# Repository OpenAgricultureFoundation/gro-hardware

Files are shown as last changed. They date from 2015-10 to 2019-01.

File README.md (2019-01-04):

# DEPRECATED.

## Personal Food Computer 1.0

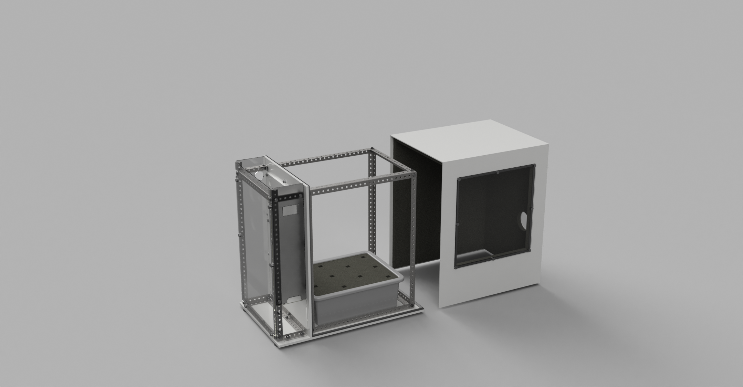
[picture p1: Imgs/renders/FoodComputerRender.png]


## Resources in this repository

- Guides
	- [Shell Assembly Guide](./Guides/ShellAssemblyGuide.md)
	- [Main Frame Assembly Guide](./Guides/MainFrameAssemblyGuide.md)
	- [Motherboard Assembly Guide(PDF only)](./Guides/PDF/MotherboardAssemblyGuide.pdf)
- CAD Models
	- [CAD Models(Solidworks)](./CAD)
	- [Laser Cutter DXF files](./CAD/LASERCUT)
	- [CNC Machine DXF Files](./CAD/CNCs)
- [Bill of Materials](./BOM.xlsx) (There are multiple sheets in the book, check bottom tabs.)

## External Links
- [Overview/Wiki](http://wiki.openag.media.mit.edu/food_computer_1)
- [Build Video](https://youtu.be/Jx-y0jQJlfs)
- ["Build" Page on OpenAg Website](http://openag.media.mit.edu/build/)
- [Adrian Lu protoshield wiring](http://adrianllu.com/2016/04/17/motherboard-build-notes-part-1-micro-controller-protoshield/)
- [JoshSinykin's wiring diagram](http://forum.openag.media.mit.edu/t/about-the-instructions-category/19/2)

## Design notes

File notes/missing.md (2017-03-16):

# Missing parts

## Not on BOM
- 6channel, maletofemale jumper wire
- screws?
  - [long    = 1.5"](http://www.homedepot.com/p/Everbilt-6-x-1-2-in-Zinc-Plated-Phillips-Pan-Head-Drive-Sheet-Metal-Screw-100-Piece-801552/204275068)
  - [medium  = 1.0"](http://www.homedepot.com/p/Everbilt-6-x-1-in-Zinc-Plated-Pan-Head-Phillips-Drive-Sheet-Metal-Screw-100-Piece-801572/204275050)
- reed relay
- GROVE connectors
  - [1 5pk female jumper to grove](https://www.seeedstudio.com/Grove-4-pin-Female-Jumper-to-Grove-4-pin-Conversion-Cable-%285-PCs-per-PAck%29-p-1020.html)
  - [1 5pk male jumper to grove cable](https://www.seeedstudio.com/Grove-4-pin-Male-Jumper-to-Grove-4-pin-Conversion-Cable-(5-PCs-per-Pack)-p-1565.html)
  - [1 5pk 4 pin, buckled, 50cm grove cable](https://www.seeedstudio.com/Grove-Universal-4-Pin-Buckled-50cm-Cable-(5-PCs-Pack)-p-928.html)
  - [1 10pk Grove connector sockets](https://www.seeedstudio.com/Grove-Universal-4-pin-connector-p-789.html)
  - [1 Grove - Temperature&Humidity Sensor Pro](https://www.seeedstudio.com/Grove-Temperature%26Humidity-Sensor-Pro-p-838.html)

# Tools

- Hole Saws

| Size | Usage |
| :--- | :--- |
| - 0.5 in  | Wire management |
| - 0.75 in | Camera |
| - 1.5 in  | Wire management|
| - 1.75 in | Heater |
| - 4.5 in  | Heater |

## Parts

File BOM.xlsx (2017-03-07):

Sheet: Motherboard
Item Name | Distributor | Distributor's Item Name | Units | Cost per Unit ($) | Item Cost
POWER
Power Strip (http://www.amazon.com/CyberPower-CSB606-Protector-6-Outlets-Joules/dp/B00FLTTGYG) | AmazonPrime | CyberPower CSB606 Surge Protector 6-Outlets 6-Ft Cord 900 Joules | 1 | 10.15 | 10.15
Main Power Supply (http://www.amazon.com/Switching-Power-Supply-Strip-Light/dp/B007MWNF5Q) | AmazonPrime | 12V 30A 360W Switching Power Supply for LED Strip Light | 1 | 24.96 | 24.96
AC Extension Cable (http://www.amazon.com/gp/product/B0002J1KS0/ref=ox_sc_act_title_1?ie=UTF8&psc=1&smid=ATVPDKIKX0DER) | AmazonPrime | C2G / Cables To Go 03137 18 AWG Outlet Saver Power Extension Cord for NEMA 5-15P to NEMA 5-15R, Black (1 Foot/0.30 Meters) | 1 | 4.99 | 4.99
BRAINS
Raspberry Pi Power Supply (http://www.amazon.com/CanaKit-Raspberry-Power-Supply-Listed/dp/B00MARDJZ4) | AmazonPrime | CanaKit 5V 2.5A Raspberry Pi 2 Power Supply (UL Listed) | 1 | 9.99 | 9.99
Arduino Mega 2560 (http://www.amazon.com/Ximico-Arduino-Cable-Atmega2560-16au-Compatible/dp/B00KG3SBE8?s=pc) | AmazonPrime | Ximico Mega 2560 R3 for Arduino + USB Cable / Mega 2560 R3 Atmega2560-16au Board (Compatible with Arduino) | 1 | 14.19 | 14.19
Raspberry Pi 2 Model B (http://www.amazon.com/Raspberry-Pi-Model-Desktop-Linux/dp/B00T2U7R7I) | AmazonPrime | Raspberry Pi 2 Model B Desktop (Quad Core CPU 900 MHz, 1 GB RAM, Linux) | 1 | 41.87 | 41.87
Micro SD Card (http://www.amazon.com/Kingston-microSDHC-Memory-SDC4-8GBET/dp/B00200K1TS?s=pc) | AmazonPrime | Kingston 8 GB microSDHC Class 4 Flash Memory Card SDC4/8GBET | 1 | 3.99 | 3.99
Ethernet cable (http://www.amazon.com/gp/product/B00EUHRLF6) | AmazonPrime |  | 1 | 5.99 | 5.99
Arduino Mega Protoshield (http://www.amazon.com/Gikfun-Protoshield-Prototype-Shield-Arduino/dp/B00Q9YBQ04?s=pc) | AmazonPrime | Gikfun Protoshield Prototype Shield DIY KIT A1 for Arduino Mega 1280 2560 R1 - R3 | 1 | 8.99 | 8.99
Grove Base Shield (https://www.seeedstudio.com/item_detail.html?p_id=1378) | SeeedStudio | Base Shield V2 | 1 | 8.9 | 8.9
Touchscreen Display (https://www.adafruit.com/products/2097) | Adafruit | PiTFT - Assembled 480x320 3.5" TFT+Touchscreen for Raspberry Pi | 1 | 44.95 | 44.95
GPIO Cable (http://www.amazon.com/ribbon-cable-Raspberry-stackable-header/dp/B00G84WNA2) | AmazonPrime | GPIO ribbon cable for Raspberry Pi set with 2x13 stackable header and 2x13 box header | 1 | 3.99 | 3.99
VOLTAGE CONTROL
4-Channel Relay (http://www.amazon.com/JBtek-Channel-Module-Arduino-Raspberry/dp/B00KTEN3TM?s=pc) | AmazonPrime | JBtek 4 Channel DC 5V Relay Module for Arduino Raspberry Pi DSP AVR PIC ARM | 2 | 6.98 | 13.96
AC Relay Box Back Receptacle (http://www.amazon.com/52171-4E-Pre-Galvanized-Eccentric-Knockouts/dp/B000HEFCKC) | AmazonPrime | Steel City 52171 1/2&3/4E Pre-Galvanized Steel Square Box with Ground Bump and 1/2-Inch and 3/4-Inch Eccentric Knockouts | 1 | 2.04 | 2.04
AC Relay Box Front Panel (http://www.amazon.com/RS8-Outlet-Surface-Square-Galvanized/dp/B000HEIU9W) | AmazonPrime | Steel City RS8 Outlet Box Surface Cover, Square, Raised, 4-Inch, Galvanized | 1 | 4.92 | 4.92
AC Plug (http://www.amazon.com/Leviton-T5320-W-Resistant-Receptacle-Residential/dp/B0015R9M2Y) | AmazonPrime | Leviton T5320-W 15 Amp, 125 Volt, Tamper Resistant, Duplex Receptacle, Residential Grade, Grounding, White | 2 | 1.19 | 2.38
AC Extension Cable (http://www.amazon.com/gp/product/B0002J1KS0/ref=ox_sc_act_title_1?ie=UTF8&psc=1&smid=ATVPDKIKX0DER) | AmazonPrime | C2G / Cables To Go 03137 18 AWG Outlet Saver Power Extension Cord for NEMA 5-15P to NEMA 5-15R, Black (1 Foot/0.30 Meters) | 1 | 4.99 | 4.99
LIGHTS
White LED Strip (http://www.amazon.com/Triangle-Bulbs-T93007-Waterproof-Flexible/dp/B005EHHLD8) | AmazonPrime | Triangle Bulbs T93007 - Waterproof Flexible LED Strip Light, 300 LED's, 3528 SMD, Pure White, 16.4 feet / 5M | 2 | 9.99 | 19.98
Grow LED Panel (http://www.amazon.com/Erligpowht-Indoor-Garden-Plant-Hanging/dp/B00S2DPYQM) | AmazonPrime | Erligpowht 45W LED Red Blue Indoor Garden Plant Grow Light Hanging Light | 2 | 37.99 | 75.98
AIR CONDITIONING
Heater (http://www.amazon.com/dp/B003XDTWN2/ref=sr_ph?&ie=UTF8&qid=1440085101&sr=1&keywords=heater) | AmazonPrime | Lasko #100 MyHeat Personal Ceramic Heater | 1 | 15.99 | 15.99
Humidifier (http://www.amazon.com/Acoustic-Audio-Tek%C2%A8Portable-Humidifier-travel--White/dp/B00RM5Z44S?s=home-garden) | AmazonPrime | Acoustic Audio Tek¨Portable Bottle Cap Air Humidifier with bottle for office home travel--White | 1 | 7.35 | 7.35
USB Wall Adapter (http://www.amazon.com/dp/B00WJW3NM4/ref=twister_B00WJW3M3Y?_encoding=UTF8&psc=1) | AmazonPrime | 3 Pcs High Quality USB Ac Universal Power Home Wall Travel Charger Adapter | 1 | 7.99 | 7.99
Circulation/Vent Fans (http://www.amazon.com/Bgears-b-Blaster-120mm-Bearing-Extreme/dp/B0043GKY1W) | AmazonPrime | Bgears b-Blaster 120mm 2 Ball Bearing High Speed Extreme Airflow Fan | 2 | 12.93 | 25.86
Fan Guards (http://www.amazon.com/Tjernlund-1519003-Wire-Fan-Guard/dp/B008RMKFTO) | AmazonPrime | Tjernlund 1519003 Wire Fan Guard, 120 mm | 2 | 2 | 4
Fan Louvres (http://www.amazon.com/Dundas-Jafine-LC4WZW-ProVent-4-Inches/dp/B0016487CC) | AmazonPrime | Dundas Jafine LC4WZW ProVent White Exhaust Cap, 4-Inches | 2 | 6.84 | 13.68
ENVIRONMENTAL SENSING
CO2 Sensor (http://www.co2meter.com/products/cozir-0-2-co2-sensor) | CO2Meter.com | COZIR Ambient 5K CO2 Sensor | 1 | 109 | 109
Air Temperature and Humidity Sensor (http://www.seeedstudio.com/depot/Grove-TemperatureHumidity-Sensor-Pro-p-838.html) | SeeedStudio | Grove - Temperature&Humidity Sensor Pro | 1 | 14.9 | 14.9
Light Intensity Sensor (http://www.seeedstudio.com/depot/Grove-Digital-Light-Sensor-p-1281.html) | SeeedStudio | Grove - Digital Light Sensor | 1 | 9.9 | 9.9
Webcam (http://www.amazon.com/gp/product/B00YCDHQ8K?psc=1&redirect=true&ref_=oh_aui_detailpage_o06_s00) | AmazonPrime | ELP 2.1mm Lens Wide Angle Webcam Low Illumination USB Camera Module for Day&night Linux Vision | 1 | 39.9 | 39.9
ENCLOSURE SENSING
Magnetic Switch (http://www.amazon.com/gp/product/B0009SUF08?keywords=reed%20switch&qid=1443805349&ref_=sr_1_1&sr=8-1) | AmazonPrime | Magnetic Switch | 1 | 7.2 | 7.2
Limit Switch (http://www.amazon.com/Micro-Limit-Switch-Roller-Action/dp/B00E0JOTV8?s=lamps-light) | Amazon | 10 Pcs Mini Micro Limit Switch Roller Lever Arm SPDT Snap Action LOT | 1 | 3.4 | 3.4
WATER CONDITIONING
Air Pump (http://www.amazon.com/gp/product/B0009YJ4N6?redirect=true) | AmazonPrime | Tetra Whisper Air Pump (Non-UL) | 1 | 9.38 | 9.38
Air Stone (http://www.amazon.com/Jardin-Aquarium-Ceramic-Diffusers-Diameter/dp/B0050HJ7Q6/ref=pd_bxgy_199_img_z) | AmazonPrime | Jardin Aquarium Fish Tank Ponds Ceramic Air Stone Diffusers, 40mm Diameter | 1 | 3.11 | 3.11
Air Pump Tubing (http://www.amazon.com/Standard-Airline-Tubing-Accessories-25-Feet/dp/B0002563MW) | AmazonPrime | Penn-Plax® Flexible Air Line Tubing for Aquariums | 1 | 4.04 | 4.04
Aquarium Pump (http://www.amazon.com/gp/product/B00EWENMAU?redirect=true) | Amazon Prime | VicTsing 80 GPH Submersible Hydroponics Aquaponics Statuary Water Fountain Pump | 1 | 7.99 | 7.99
Pump Tubing (http://www.amazon.com/gp/product/B0079QUTSQ?redirect=true) | Amazon Prime | Hydrofarm HGTB50GF 1/2-Inch Black Tubing, 25 foot Roll | 1 | 14.39 | 14.39
WATER SENSING
Water Temperature and EC Sensor (http://www.dfrobot.com/index.php?route=product/product&product_id=1123&search=DFR0300#.VdTDoFNViko) | DFRobot | Analog Electrical Conductivity Meter (With Temperature Compensation) | 1 | 69.9 | 69.9
pH Sensor (http://www.dfrobot.com/index.php?route=product/product&product_id=1025#.Vg60SBNViko) | DFRobot | Analog pH Meter Kit | 1 | 29.5 | 29.5
ENCLOSURES
Cable Management Box (http://www.amazon.com/gp/product/B00BL63ZU4?psc=1&redirect=true&ref_=oh_aui_detailpage_o01_s00) | AmazonPrime | ORICO PB3218 Power Strip Cord Management Box Cable Box Cable Storage Box (Black) | 1 | 19.99 | 19.99
ADDITIONAL COMPONENTS
Sacrificial AC Extension Cable for high gauge wire (http://amzn.com/B002MAPS8K) | AmazonPrime | C2G / Cables To Go 53408 18 AWG Outlet Saver Power Extension Cord for NEMA 5-15P to NEMA 5-15R, Black (12 Feet/3.65 Meters) | 1 | 10.93 | 10.93
Wago Lever Nut Assortment (http://www.amazon.com/Wago-222-412-222-413-Lever-Nut-Assortment/dp/B00U4520JK) | AmazonPrime | Wago (25) 222-412 (25) 222-413 (20) 222-415 Lever-Nut Assortment Pack | 1 | 39.99 | 39.99
Heat Shrink Tubing (http://www.amazon.com/Vktech-150pcs-Shrink-Tubing-Sleeving/dp/B00EXLPLTW) | AmazonPrime | Vktech 150pcs 2:1 Heat Shrink Tubing Tube Sleeving Wire Cable 8 Sizes 2-13mm Black | 1 | 6.2 | 6.2
Grove Cables (http://www.seeedstudio.com/depot/Grove-c-98_106_57/?ref=crumb) | SeeedStudio | Buy an assortment of 10-50cm grove cables for this build. The 50cm cables
 |  | are better for the sensors and the shorter cables can be used as needed.
Foam mounting tape (http://www.homedepot.com/p/3M-Scotch-1-in-x-12-5-yds-Indoor-Outdoor-Mounting-Tape-411-LONG-DC/100153200) | Home Depot | Foam Mounting Tape | 1 | 15.97 | 15.97
Electrical Tape (http://www.amazon.com/3M-Electrical-75-Inch-66-Foot-0085-Inch/dp/B00004WCCP?s=industrial) | Amazon | Electrical Tape | 1 | 3.98 | 3.98
Air Exchange Box (http://www.digikey.com/product-search/en?KeyWords=377-2132-ND&WT.z_header=search_go) | Digikey | Plastic Box | 1 | 29.5 | 29.5
Short Screws (http://www.homedepot.com/p/Everbilt-6-x-1-2-in-Stainless-Steel-Pan-Head-Phillips-Sheet-Metal-Screw-50-per-Pack-800162/204275035) | Home Depot | #6 x 1/2 in. Stainless Steel Pan-Head Phillips Sheet Metal Screw (50 per Pack) | 1 | 5.8 | 5.8
Long Screws (http://www.homedepot.com/p/Everbilt-8-x-2-in-Zinc-Plated-Pan-Head-Phillips-Drive-Sheet-Metal-Screw-50-Piece-801632/204275094) | Home Depot | #8 x 2 in. Zinc-Plated Pan-Head Phillips Drive Sheet Metal Screw (50-Piece) | 1 | 3.51 | 3.51
TOTAL COMPONENTS |  |  | 54 | 840.56 | 840.56

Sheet: Hardware
ITEM NO. | PART NAME | PART USED FOR… | QTY. NEEDED | SOURCE | QTY. PER PACKAGE | PRICE ($) | NOTES
1 | Acrylic sheet, clear, 0.22" thick, 24" x 48" | upper front plate, lower front plate, back plate | 1 | Lowe's (http://www.lowes.com/pd_11288-1638-1AG2196A___?productId=3502046&pl=1&Ntt=.22+acrylic+sheet) | 1 | 57.98
2 | Corrugated plastic, white, 0.157" thick, 48" x 96" | plastic box | 1 | Home Depot (http://www.homedepot.com/p/Coroplast-48-in-x-96-in-x-0-157-in-White-Corrugated-Plastic-Sheet-CP4896S/205351385) | 1 | 15.98
3 | Foam, pink, 1" thick, 24" x 24" | plant tray | 1 | Home Depot (http://www.homedepot.com/p/Project-Panels-2-ft-x-2-ft-Project-Panel-PP1/203553730?keyword=foam+project+panel) | 1 | 5.48
4 | Foot pads | for bottom of PVC feet | 6 | Home Depot (http://www.homedepot.com/p/Everbilt-2-in-Self-Adhesive-Anti-Skid-Surface-Pads-8-per-Pack-49971/203661153) | 8 | 2.48
5 | Frosted glass spray paint | upper front plate, lower front plate | 1 | Home Depot (http://www.homedepot.com/p/Rust-Oleum-Specialty-11-oz-Frosted-Glass-Spray-Paint-1903830/100195608) | 1 | 3.76
6 | Hex bolts, 3/8"-16, 1 1/2" long | motherboard panel to motherboard dock panel mounting | 6 | Home Depot (http://www.homedepot.com/p/Everbilt-3-8-in-16-tpi-x-1-1-2-in-Stainless-Steel-Hex-Bolt-804316/204633369) | 1 | 1.5
7 | Hex bolts, 3/8"-16, 1" long | PVC to punched angle connections | 26 | McMaster (http://www.mcmaster.com/) | 25 | 15.88
8 | Hex bolts, 3/8"-16, 1/2" long | punched angle to punched angle connections | 46 | McMaster (http://www.mcmaster.com/) | 25 | 11.76
9 | Loctite spray glue | attach plastic box to foam box | 1 | Home Depot (http://www.homedepot.com/p/Loctite-13-5-oz-High-Performance-Spray-Adhesive-1408028/202365672) | 1 | 7.97
10 | Neodymium magnets | attaching window, lower front plate, and side plate | 44 | Home Depot (http://www.homedepot.com/p/MASTER-MAGNETICS-0-7-in-Neodymium-Rare-Earth-Magnet-Discs-3-per-Pack-07047HD/202526369) | 3 | 59.7
11 | Nuts, 3/8"-16 | back of each hex bolt | 83 | Home Depot (http://www.homedepot.com/p/Everbilt-3-8-in-16-tpi-Zinc-Plated-Hex-Nut-100-Piece-per-Box-801750/204274086) | 100 | 9.57
12 | Polycarbonate sheet, 0.093" thick, 48" x 36" | window, side plate | 1 | Home Depot (http://www.homedepot.com/p/LEXAN-48-in-x-36-in-x-093-in-Polycarbonate-Sheet-GE-38/202038065) | 1 | 72.73
13 | Punched angle, 1 1/4" x 48" | material for metal frame | 10 | Home Depot (http://www.homedepot.com/p/Crown-Bolt-1-1-4-in-x-48-in-Zinc-Plated-Punched-Angle-41790/202183466) | 1 | 94.8
14 | Punched flat, 1 3/8", 36" | LED panel mounting | 2 | Home Depot (http://www.homedepot.com/p/Everbilt-1-3-8-in-x-36-in-Zinc-Plated-Punch-Flat-Bar-800337/204325640) | 1 | 9.76
15 | PVC sheet, white, 1/2" thick, 24" x 96" | base board, motherboard panel, motherboard dock panel, feet | 1 | Home Depot (http://www.homedepot.com/p/Veranda-HP-1-2-in-x-48-in-x-8-ft-White-PVC-Trim-H120AWS6/205309788) | 1 | 43 | * link is to 48" x 96" because 24" x 96" is in stores but not online
16 | Reservoir bin | holds water for hydroponic system | 1 | Amazon Prime (http://www.amazon.com/gp/product/B000BC5EP8?psc=1&redirect=true&ref_=oh_aui_detailpage_o02_s00) | 1 | 13.75
17 | Threaded rod, 3/8", 36" | LED panel mounting | 1 | Home Depot (http://www.homedepot.com/p/Crown-Bolt-3-8-in-x-36-in-Zinc-Threaded-Rod-17340/202183465) | 1 | 2.87
18 | TUFF-R insulation, 1" thick, 48" x 96" | foam box | 1 | Home Depot (http://www.homedepot.com/p/Super-TUFF-R-1-in-x-4-ft-x-8-ft-R-6-5-Insulating-Sheathing-268426/100322374) | 1 | 18.85
19 | Washers, 3/8" | for most bolt connections | 84 | Home Depot (http://www.homedepot.com/p/Crown-Bolt-3-8-in-Zinc-Plated-Cut-Washer-100-per-Box-46060/203639706) | 100 | 10.98
20 | Weatherstrip Tape, 120" | for jacket and window seals | 2 | Home Depot (http://www.homedepot.com/p/Frost-King-E-O-9-16-in-x-5-16-in-x-10-ft-Gray-EPDM-Cellular-Rubber-Weatherstrip-Tape-V27GA/100546771) | 1 | 16.74
21 | Foil Tape |  |  |  | TOTAL | 475.54
22 | PVC standoff 2" Diameter

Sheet: Kit
ITEM NO. | PART NAME | PART USED FOR… | QTY. NEEDED | SOURCE | QTY. PER PACKAGE | PRICE
1 | General Hydroponics pH Control Kit | pH balancing of the water | 1 | Amazon Prime (http://www.amazon.com/General-Hydroponics-GH1514-Control-Kit/dp/B000BNKWZY?s=lawn-garden) | 1 | 16.21
2 | Fertilizer 5-12-26 | plant nutrients | 1 | JRPeters (http://www.jrpeters.com/Products/Hydroponics/Buy-Hydroponics.html) | 4 lbs | 29.99
3 | Fertilizer 15-0-0 | plant nutrients | 1 | JRPeters (http://www.jrpeters.com/Products/Hydroponics/Buy-Hydroponics.html) | 4 lbs | 29.99
4 | Gloves | PPE | 1 | Amazon Prime (http://www.amazon.com/Clean-Ones-Disposable-Essentials-Latex-free/dp/B00D8I346S) | 100 ct | 9.99
5 | Safety glasses | PPE | 1 | Amazon Prime (http://www.amazon.com/Pyramex-S4110SMP-Safety-Glasses-Intruder/dp/B002KA00KS) | 6 | 12.28
6 | Pipettes | water chemistry balancing | 10 | Amazon Prime (http://www.amazon.com/gp/product/B005IQTSE0) | 100 | 4.5
7 | Yeast | carbon dioxide bioreactor | 1 | Amazon (http://www.amazon.com/Fleischmanns-Active-Yeast-0-75-Packet/dp/B0014CTFU4?s=aps) | 3 | 3.99
8 | Sugar | feeds the yeast | 1 | Amazon (http://www.amazon.com/Domino-Sugar-Granulated-10-Pound-Bags/dp/B00060N5OW?s=grocery) | 1 | 15.09
9 | Bottles | holding yeast bioreactor, fertilizers, sugar | 6 | Amazon Prime (http://www.amazon.com/gp/product/B00YQLI1KK?psc=1&redirect=true&ref_=oh_aui_detailpage_o02_s01) | 10 | 19.95
10 | Tubing | from yeast bioreactor to grow chamber | 2' | Amazon Prime (http://www.amazon.com/Watts-SVGE10-Pre-Cut-Diameter-10-Foot/dp/B000HE5DUG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) | 10' | 7.31
11 | One-way valve | allows carbon dioxide to flow towards the chamber, but nothing into the bioreactor | 1 | Amazon (http://www.amazon.com/Inside-Diameter-Plastic-One-way-Check/dp/B005OUKJ1Q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) | 4 | 2.85
12 | Horticubes | plants' growth substrate | 1 | Amazon Prime (http://www.amazon.com/Grodan-Rockwool-Stonewool-Cuttings-Propagation/dp/B0087SJ3U0) | 200 | 18
13 | Measuring spoons | measure out fertilizers, yeast, and sugar | 1 | Amazon Prime (http://www.amazon.com/Good-Cook-Classic-Plastic-Measuring/dp/B000BQKVQ6?s=aps) | 1 | 3.97
 |  |  |  |  | TOTAL | 174.12

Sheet: Tools
Hand Tools | Shop Tools | Personal Protective Equipment
3/8 Ratchet | bandsaw | safety goggles
crescent wrench | laser cutter | ear protection
Hot glue | shopbot
Soldering iron | table saw
VHB tape | grinding wheel
Electrical tape
Wire strippers
Philips head screwdrivers (multiple sizes)
power drill
driving bits
drill bit set
Hole saw set (up to 4" diameter)
Multimeter
Wire wrapping tool
solder
wire wrapping wire
hobby knife
dykes
pliers
file
sandpaper
deburring tool
lighter
sharpie

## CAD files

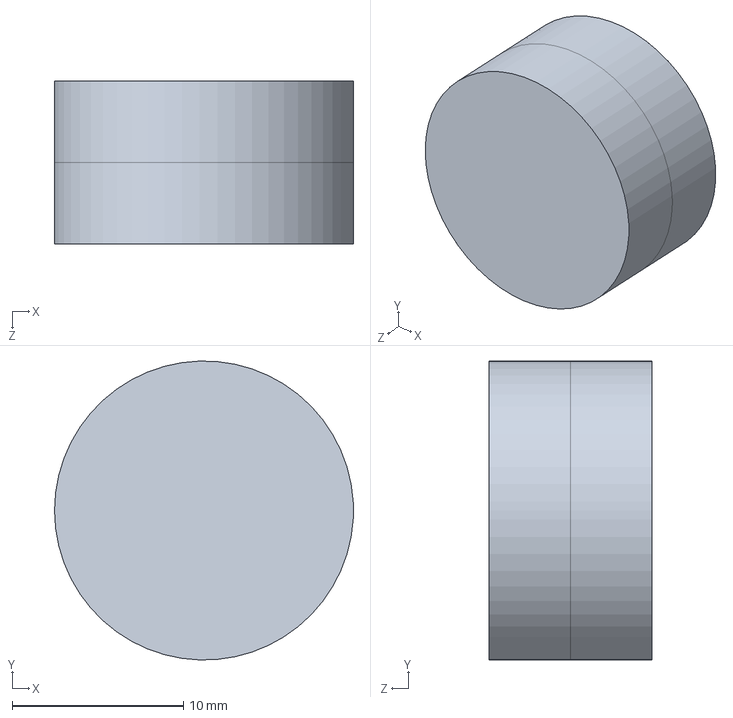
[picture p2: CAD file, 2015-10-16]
CAD/SUBASSEMBLIES/Double magnet SubAssem.SLDASM
17.5 x 17.5 x 9.52 mm
disc magnet x 2

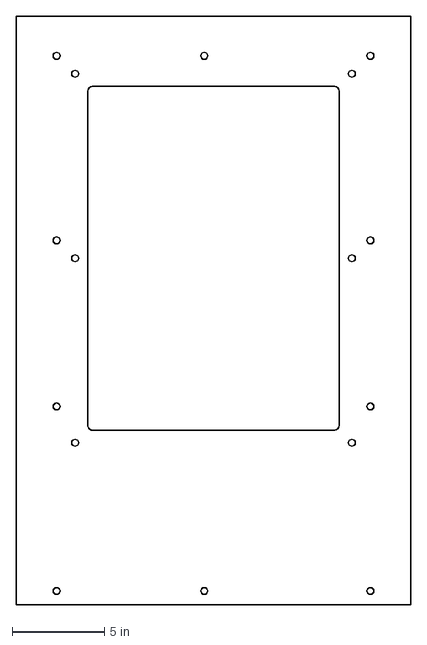
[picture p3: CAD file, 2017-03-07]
CAD/CNC/MainFrame.dxf
21.4 x 31.9 in

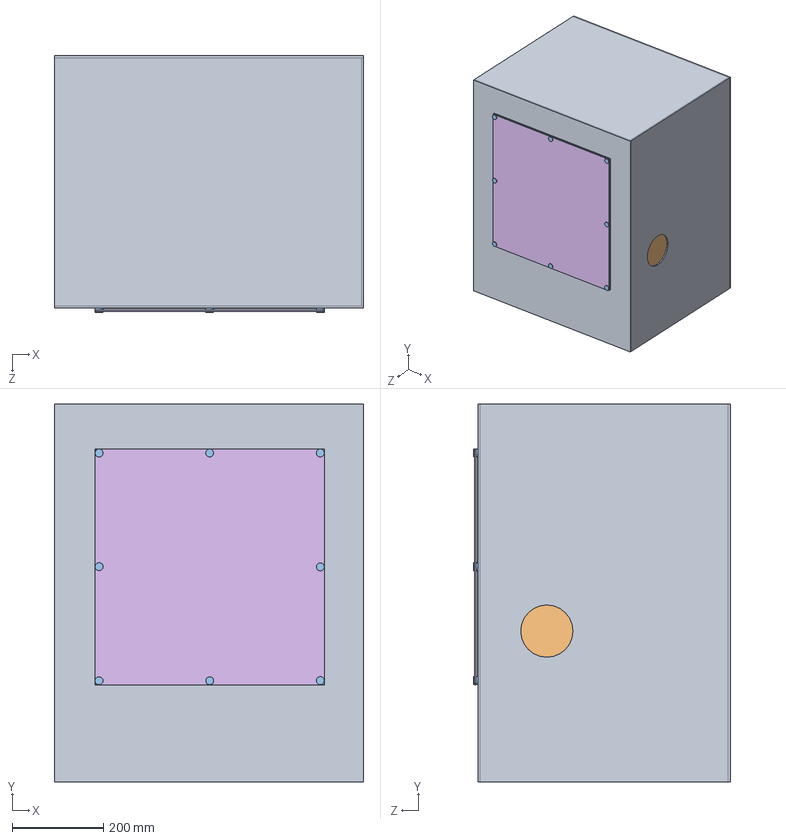
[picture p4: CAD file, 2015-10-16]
CAD/SUBASSEMBLIES/Jacket SubAssem.SLDASM
676.3 x 827.1 x 562.0 mm
foam box
plastic box
disc magnet x 24
weatherstrip window horiz x 4
weatherstrip window vert x 4
window

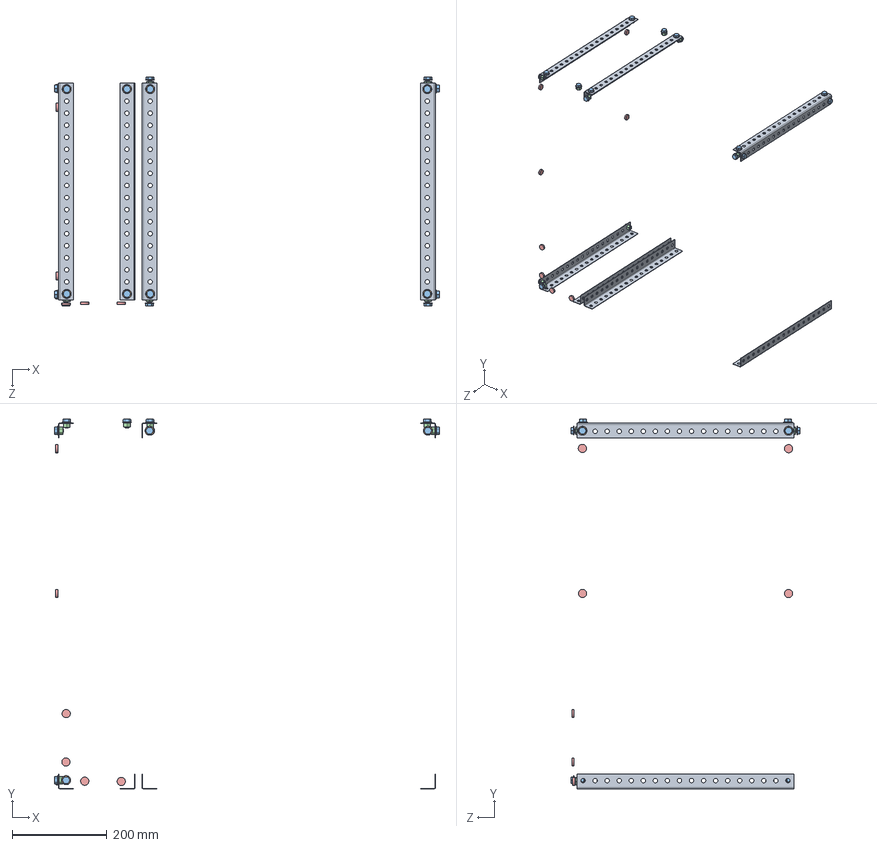
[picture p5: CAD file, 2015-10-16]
CAD/SUBASSEMBLIES/Metal Frame SubAssem.SLDASM
811.5 x 779.4 x 483.2 mm
punched angle 18L x 7
washer 3-8 x 19
hex bolt 3-8 1-2L x 19
hex nut 3-8 x 19
disc magnet x 10

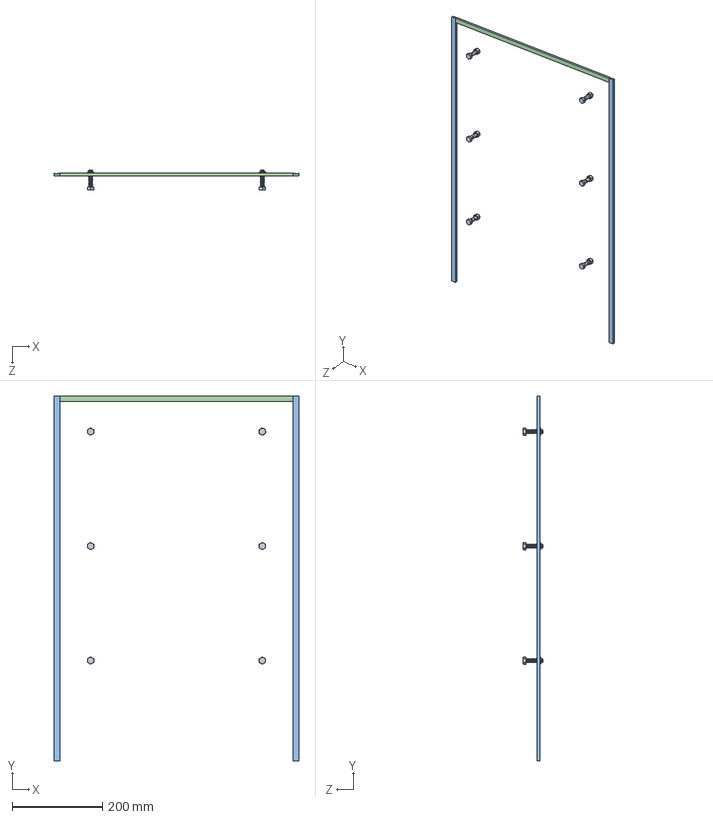
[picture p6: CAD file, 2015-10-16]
CAD/SUBASSEMBLIES/Motherboard SubAssem.SLDASM
542.9 x 809.6 x 44.1 mm
hex bolt 3-8 1 1-2L x 6
hex nut 3-8 x 6
weatherstrip motherboard vert x 2
weatherstrip depth

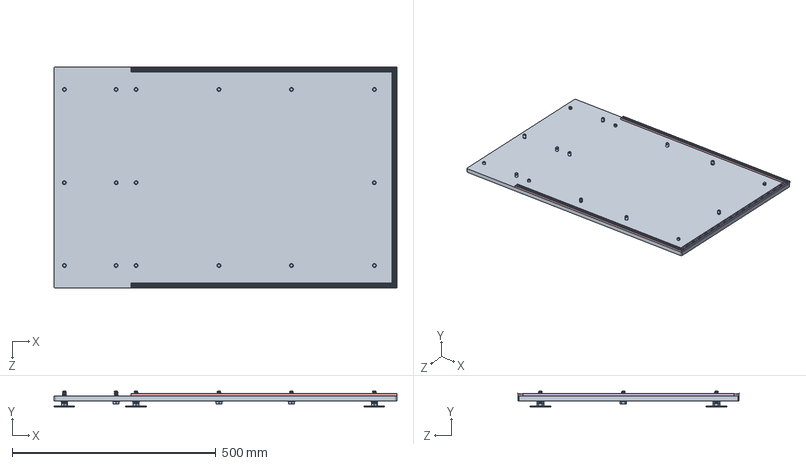
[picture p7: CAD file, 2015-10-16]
CAD/SUBASSEMBLIES/Base SubAssem.SLDASM
841.1 x 38.7 x 542.9 mm
base board
foot pad x 6
hex bolt 3-8 1L x 16
washer 3-8 x 10
weatherstrip base horiz x 2
weatherstrip depth

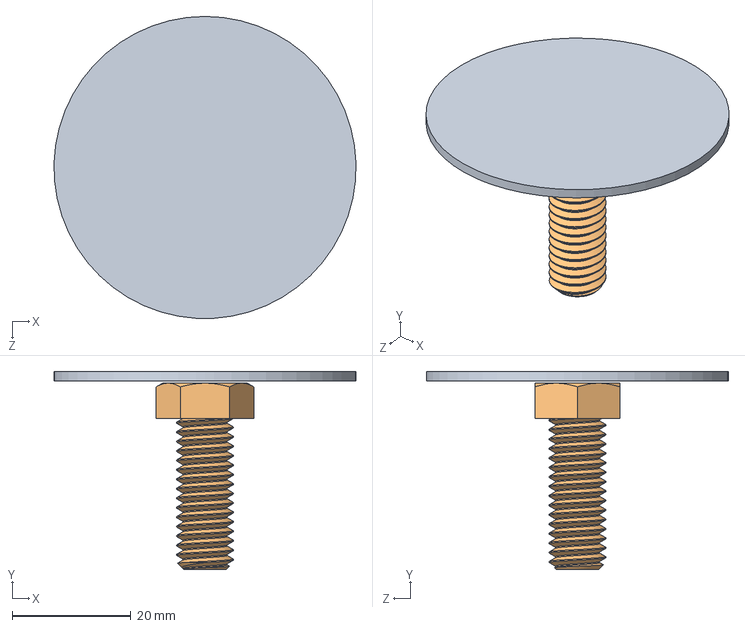
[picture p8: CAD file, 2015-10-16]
CAD/SUBASSEMBLIES/Foot SubAssem.SLDASM
50.8 x 33.3 x 50.8 mm
foot pad
hex bolt 3-8 1L

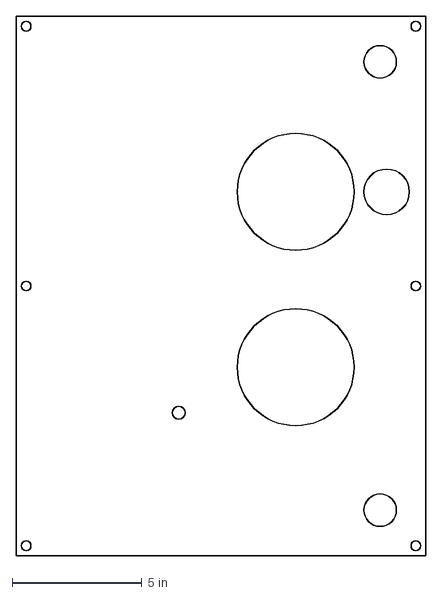
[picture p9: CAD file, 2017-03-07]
CAD/CNC/MotherBoard.dxf
15.7 x 20.7 in

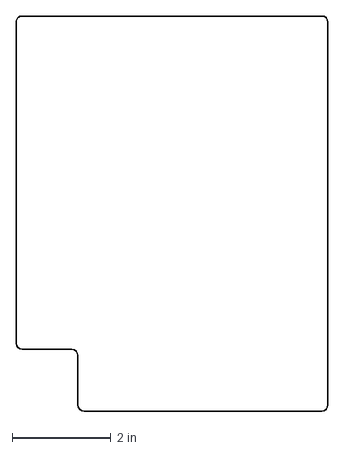
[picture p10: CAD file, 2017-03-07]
CAD/LASERCUT/front-lower-plate.dxf
6.31 x 8.00 in

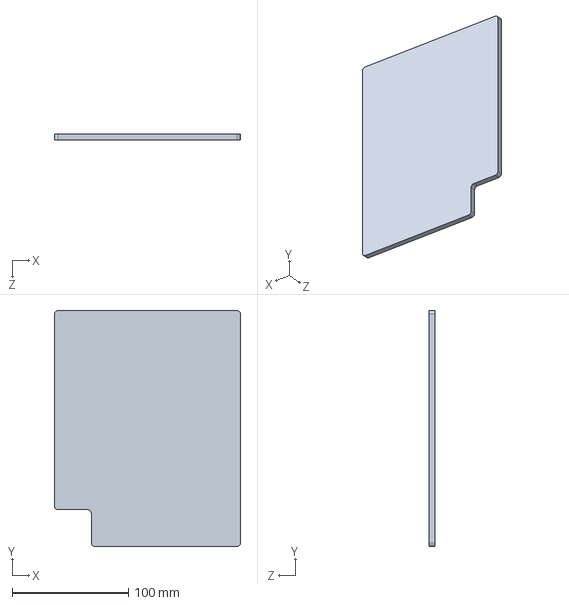
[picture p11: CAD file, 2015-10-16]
CAD/PARTS/ACRYLIC/lower front plate/lower front plate.SLDPRT
160.3 x 203.2 x 5.59 mm

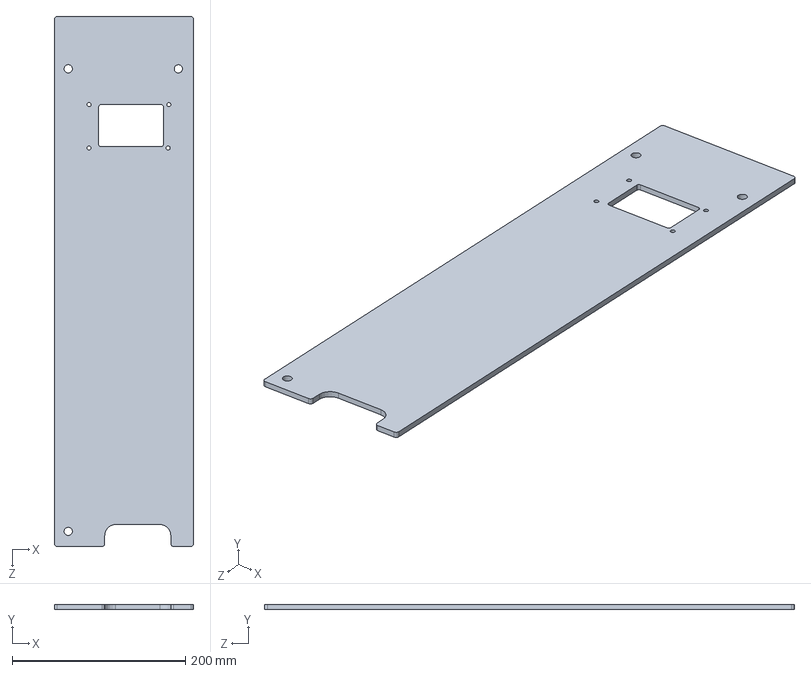
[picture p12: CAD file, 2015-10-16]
CAD/PARTS/ACRYLIC/upper front plate/upper front plate.SLDPRT
160.3 x 5.59 x 611.2 mm

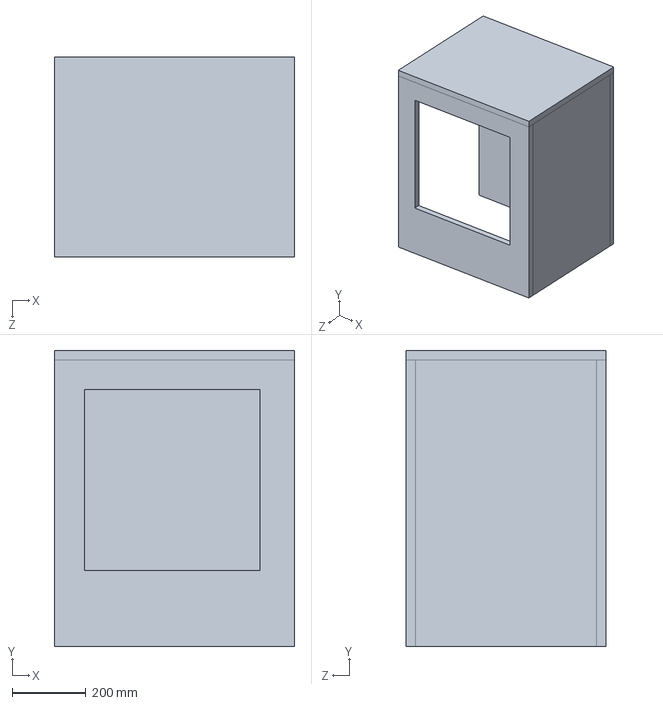
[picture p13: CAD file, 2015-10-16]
CAD/PARTS/foam box/foam box.SLDPRT
652.5 x 803.3 x 542.9 mm

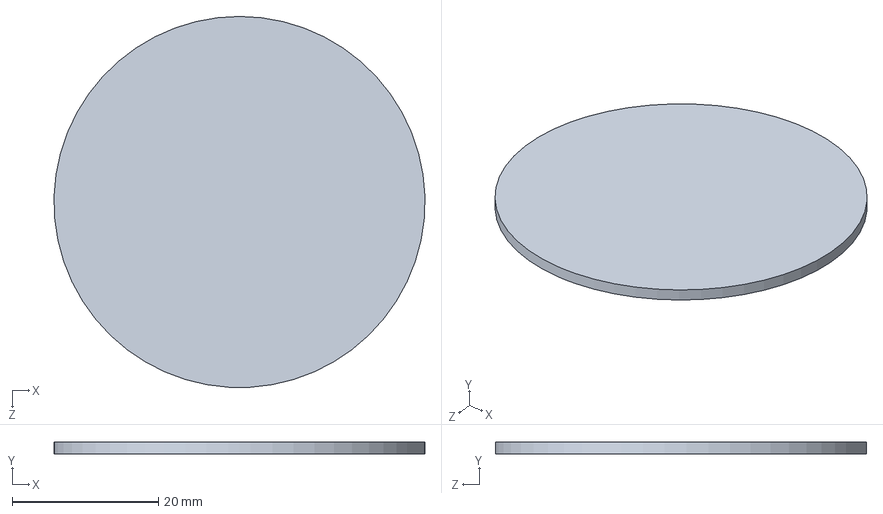
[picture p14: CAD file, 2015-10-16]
CAD/PARTS/foot pad/foot pad.SLDPRT
50.8 x 1.59 x 50.8 mm

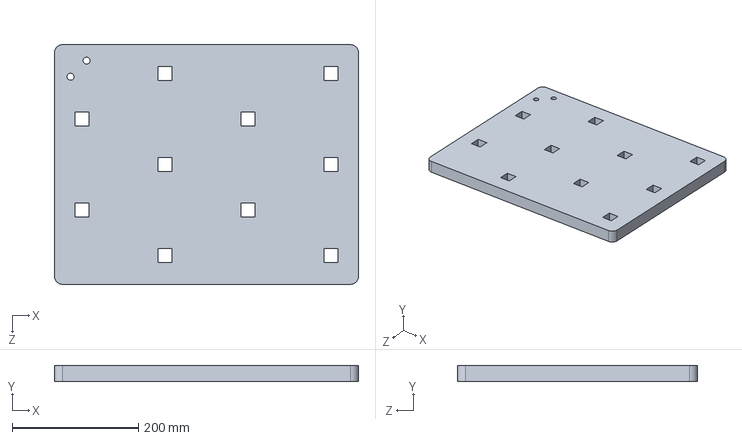
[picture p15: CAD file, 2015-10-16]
CAD/PARTS/plant tray/plant tray.SLDPRT
481.0 x 25.4 x 379.4 mm

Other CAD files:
CAD/Food Computer Assembly.SLDASM
CAD/PARTS/plastic box/plastic box.SLDPRT
CAD/PARTS/POLYCARBONATE/back plate/back plate.SLDPRT
CAD/PARTS/POLYCARBONATE/side plate/side plate.SLDPRT
CAD/LASERCUT/back-plate.dxf
CAD/LASERCUT/front-upper-plate.dxf
CAD/LASERCUT/side-plate.dxf
CAD/PARTS/FASTENERS/disc magnet/disc magnet.SLDPRT
CAD/PARTS/FASTENERS/hex bolt 3-8 1 1-2L/hex bolt 3-8 1 1-2L.SLDPRT
CAD/PARTS/FASTENERS/hex bolt 3-8 1-2L/hex bolt 3-8 1-2L.SLDPRT
CAD/PARTS/FASTENERS/hex bolt 3-8 1L/hex bolt 3-8 1L.SLDPRT
CAD/PARTS/FASTENERS/hex nut 3-8/hex nut 3-8.SLDPRT
CAD/PARTS/FASTENERS/washer 3-8/washer 3-8.SLDPRT
CAD/PARTS/POLYCARBONATE/window/window.SLDPRT
CAD/PARTS/PUNCHED ANGLE/punched angle 18L/punched angle 18L.SLDPRT
CAD/PARTS/PUNCHED ANGLE/punched angle 24L/punched angle 24L.SLDPRT
CAD/PARTS/PUNCHED ANGLE/punched angle 30 1-2L/punched angle 30 1-2L.SLDPRT
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

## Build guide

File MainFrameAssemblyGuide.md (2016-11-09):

# Main Frame Assembly Guide

## Parts

  * PVC base board
  * PVC motherboard wall
  * 6 x 2” diameter PVC standoffs
  * 6 x 2” self adhesive anti­skid surface pads Punched angle
    * 2 x 31 1⁄2” 4 x 30”
    * 4 x 24”
    * 7 x 18”
    * 4 x 6”
    * 2 x 1”
  * 26 x 3⁄8”­16 1” bolts
  * 46 x 3⁄8”­16 1⁄2” bolts 83 x 3⁄8”­16 nuts
  * 84 x 3⁄8” washers
  * 10’ weatherstrip tape

## Tools

  * 3⁄8” ratchet
  * 3⁄8” crescent wrench

## Instructions

1.   Place the PVC base board on a flat surface with the faux wood side down. The 6 holes on the left side outline the base of the electronics chamber, and the 10 holes on the right side outline the base of the grow chamber.

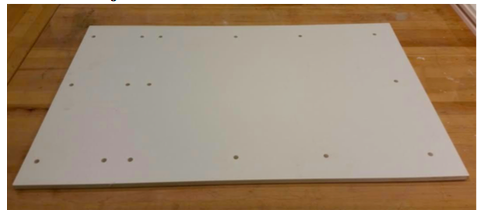
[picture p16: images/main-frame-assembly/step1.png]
    

2.  Lay out 2 of the 6” punched angle lengths electronics side and 2 of the 24” punched angle lengths on the grow side as shown.

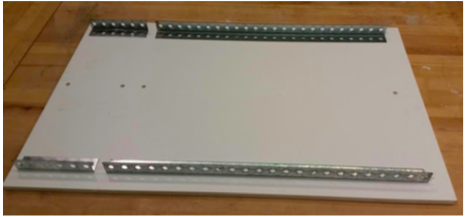
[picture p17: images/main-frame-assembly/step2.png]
    

3.  Lay out 2 of the 18” punched angle lengths on the outermost sides of the base board and another on the right side of the electronics chamber side as shown. Secure this base frame with the 1” bolts on all non­corner through holes. Use washers on both sides of the board and put the heads of the bolts on the underside of the board.

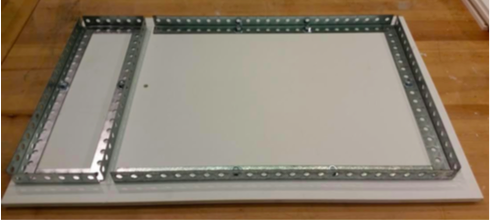
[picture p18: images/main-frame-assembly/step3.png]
    

4.  Place 1” bolts through 4 of the standoffs making sure the heads of the bolts are on the countersunk side of the standoffs.

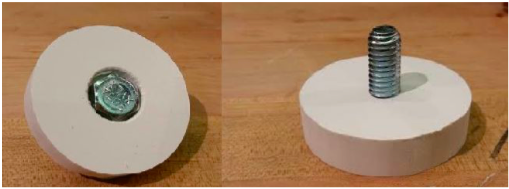
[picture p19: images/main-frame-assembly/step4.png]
    

5.  Insert these standoffs through the 4 outermost corner holes of the base board with the standoffs on the underside of the base board. Do not use washers on either side of the bolt. Make sure the bottom of your base board matches the picture below.

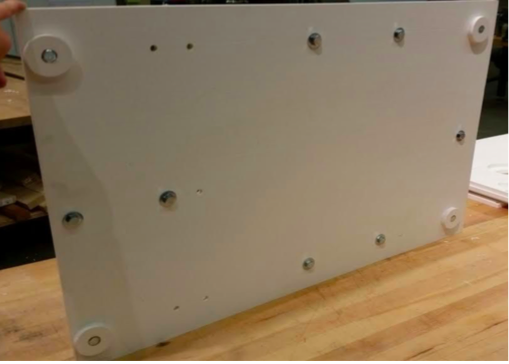
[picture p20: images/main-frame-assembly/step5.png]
    

6.  Set the PVC motherboard wall on the table with the faux wood side down. Place 2 of the 30” punched angle lengths along the length of the board. Use 1” bolts with washers on each side to secure the 30” lengths to the board through the 4 aligning non­corner through holes. Orient the bolts such that heads are on the punched angle side of the wall.

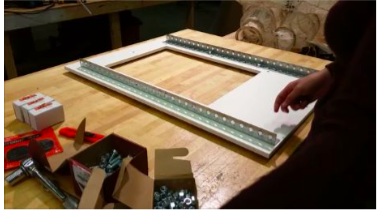
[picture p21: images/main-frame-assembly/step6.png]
    

7.  Place 1 of the 18” punched angle lengths along the top of the motherboard wall and use a 1” bolt to secure the 18” length at its center through the PVC motherboard wall.

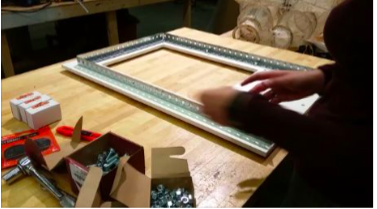
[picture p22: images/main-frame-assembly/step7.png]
    

8.  Now align the motherboard wall perpendicular to the base board, with the punched angle parts secured to the motherboard wall facing the grow chamber side as shown. Place 1 more of the 18” punched angle lengths at the base of the motherboard wall on the grow chamber side. Secure the 18” length to the motherboard wall and 18” length on the other side using 1” bolts with no washers at the two bottom corners and single center through hole. Orient the bolts such that heads are on the grow side of the motherboard wall.

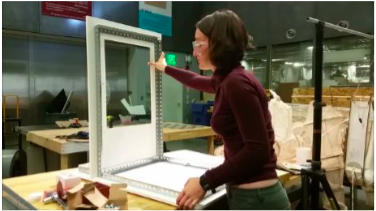
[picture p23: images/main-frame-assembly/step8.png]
    

9.  Set the frame on its side to insert the last standoffs and 1” bolts through the base board such that the bottom looks as shown. For the last 2 standoffs, do not use washers. For the rest, use washers only on the bottom of the base board. Tighten all bolts and standoffs with the ratchet and crescent wrench.

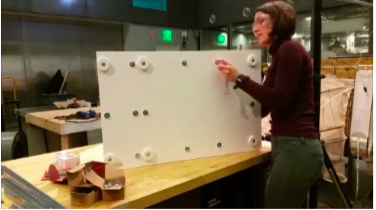
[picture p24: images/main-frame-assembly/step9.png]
    

10.   Peel the paper off the backs of the 6 anti­skid pads and stick them to the standoffs as shown.

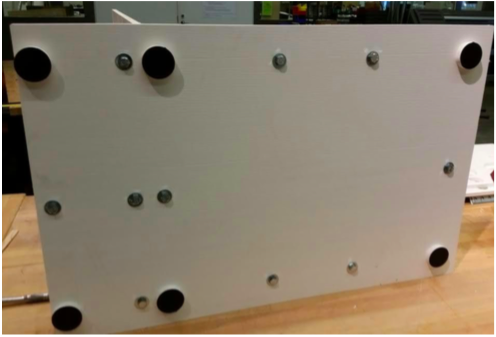
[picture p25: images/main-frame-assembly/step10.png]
    

11.   Put the 1” angle brackets on the bolt ends on the electronics side of the motherboard wall. Orient the brackets as shown below. Secure each end with 1” bolts and no washers.

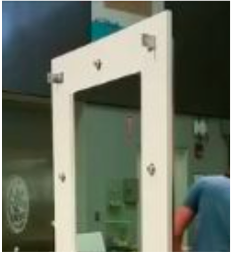
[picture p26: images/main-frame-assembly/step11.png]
    

12.   Use the 2 30 1⁄2” punched angle lengths as the vertical posts on the outermost electronics chamber side, making sure that the end of the length with the cut through a punched hole is towards the top. Use the 1⁄2” bolts to secure the bases, with washers on the outside but not the inside of the punched angle corners. Make sure the intersections between angle parts are approximately perpendicular.

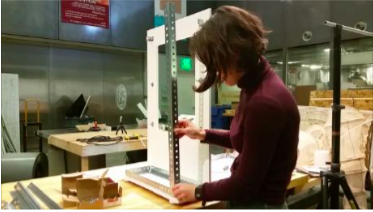
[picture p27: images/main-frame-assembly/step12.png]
    

13.   Use the last 2 30” punched angle lengths for the outermost vertical posts on the grow chamber side of the frame. Again, use 1⁄2” bolts with washers on the outside and not the inside of the punched angle corners. Make sure the intersections between angle parts are approximately perpendicular.

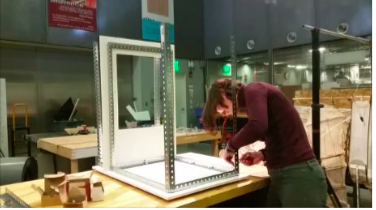
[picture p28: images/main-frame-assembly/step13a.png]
    

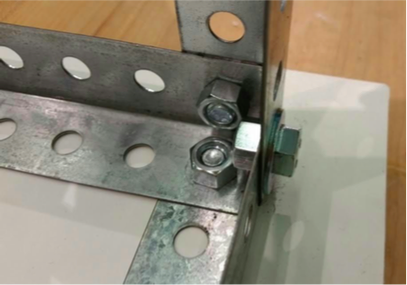
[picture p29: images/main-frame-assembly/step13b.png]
    

14.   Install the top 18” angle part depths on the farthest left and right sides of the assembly with the 1⁄2” bolts with washers on the outside head sides of the bolts. Install the top 6” widths on the electronics chamber side, securing the two outer corners with 1⁄2” bolts with washers on the top side.

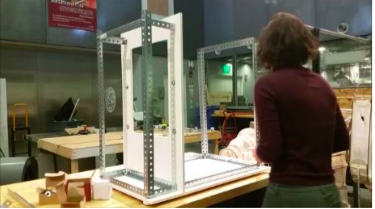
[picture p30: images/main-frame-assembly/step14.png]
    

15.   Place the grow side top width 24” angle parts, making sure they are placed above the 18” top depth parts but inside the vertical posts.

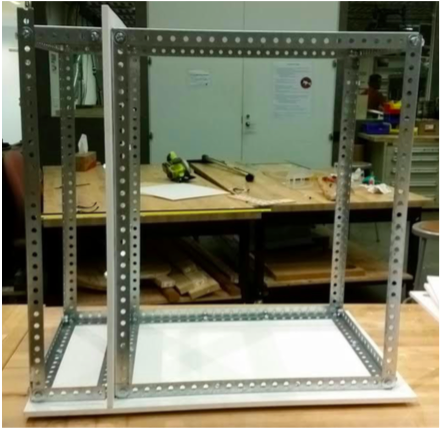
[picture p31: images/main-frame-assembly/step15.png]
    

16.   Get a top­down view of the assembly now, by either standing on the table or bringing the assembly down onto the floor. Secure the 6 corners with the last 1⁄2” bolts, with heads and washers on the top of the frame and nuts without washers on the underside.

17.   Do some last adjusting if the frame is crooked. Check each corner to make sure all pairs of angle bracket are perpendicular to each other. You may have to do some loosening and retightening of bolts.

18.   Now to make the seal between the main frame and jacket. Take your weatherstripping and line the base of the PVC base board on the grow side with it. Make sure the edge of the weatherstripping is right along the edge of the base but not protruding over the edge as this will make sliding the clam shell jacket over difficult or impossible. Do the same along the edge of the grow side of the PVC motherboard wall.

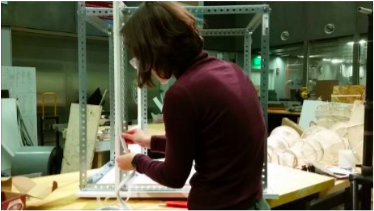
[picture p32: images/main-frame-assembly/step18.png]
    

19.   Now, weatherstrip around the edge of the PVC motherboard wall cutout on the electronics chamber side. This will act as the seal when the electronics panel is pressed against the weatherstripping and bolted onto the motherboard wall.

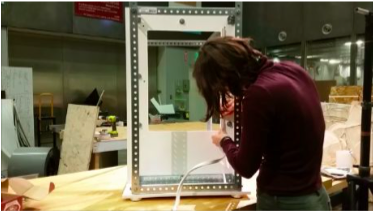
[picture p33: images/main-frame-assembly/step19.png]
    

20.   Take the laser cut front upper plate and back plate and install onto front and back faces of the punched angle frame on the electronics side, respectively. Use the 1⁄2” bolts and washers on the outer face and just nuts on the inner face.

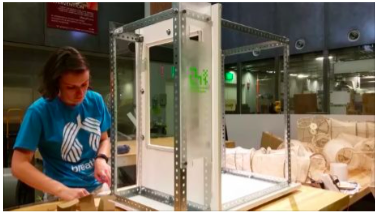
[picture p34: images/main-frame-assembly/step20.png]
    

21.   Find 20 of the magnets and put VHB tape onto one side, making sure the polarity orientation is the same for all 20. Tape 4 of the magnets along the punched angle that outlines the place of the front lower plate and 6 of the magnets along the punched angle that outlines the place of the side plate.

22.   Put the front lower plate against the punched angle, and align another set of magnets with those taped directly to the punched angle. Tape the new magnets onto the front lower plate.

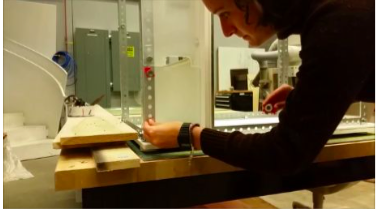
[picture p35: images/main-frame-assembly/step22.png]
    

23.   Do the same with the last 6 magnets and the side plate.

## Assemble the kit section

This is the “wet lab” section that sits underneath the electronics motherboard. It contains the materials for water chemistry balancing and managing a yeast reactor and also includes some safety equipment.

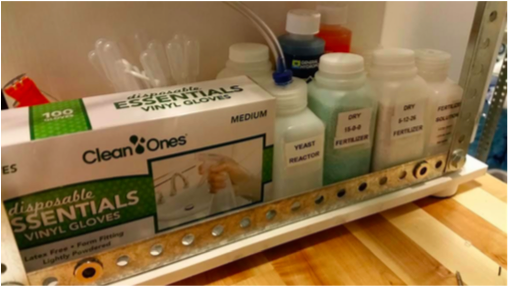
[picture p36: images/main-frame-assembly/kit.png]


Yeast reactor: Drill a 3⁄8” hole in the lid of the bioreactor bottle. Hot glue the one­way valve into the opening, making sure that the arrow on the valve is pointing upwards, out of the bottle. Cut 2’ of the 3⁄8” tubing and push one end onto the one­way valve and route the other through the bottom left hole in the electronics panel through to the grow chamber side. The bottle behind the yeast reactor is filled with sugar.

To the right of the yeast reactor bottle are the four fertilizer bottles. Two contain dry fertilizer while the other two contain solutions of the fertilizers in water. Behind those fertilizer bottles sits the pH balancing kit.

Not seen behind the box of gloves are extra packets of yeast, measuring spoons, safety glasses, and pipettes.

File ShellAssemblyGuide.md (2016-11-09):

# Shell Assembly Guide

## Cutting the Insulation Foam

If you are cutting using a standard table saw, I found that it is easier to cut the large 4’x8’ sheet into sections slightly larger than the ultimate panel dimensions. This both makes each individual panel easier to work with and provides a clean opposite to the final cut width.

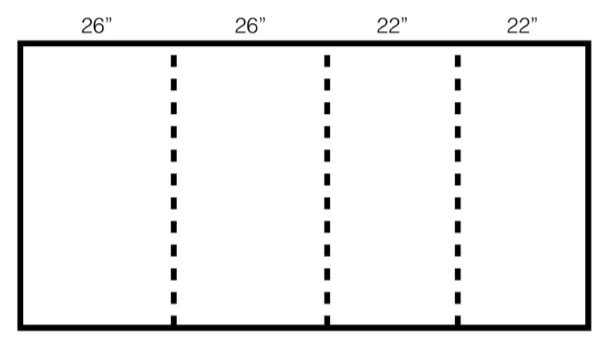
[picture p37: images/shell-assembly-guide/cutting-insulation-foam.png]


Once the sheets have been cut into the approximate panel dimensions, you can then cut the actual dimensions in the CAD.

```
Front Panel: 25.6875” x 30.625”
Back Panel: 25.6875” x 30.625”
Side Panel: 19.375” x 30.625”
Top Panel: 21.375” x 25.6875”
```

Next you need to cut the window into the front panel. I created a jig but a ruler works just fine. From the upper left corner as the origin of a cartesian system, measure 3.25” in the +x direction and 3.1875 in the ­y direction. This will be the upper left corner of the window. The dimensions of the window are 18.75” wide by 19.3125” tall. See picture below for relative orientation if confused. Cut out the window and discard the scrap.

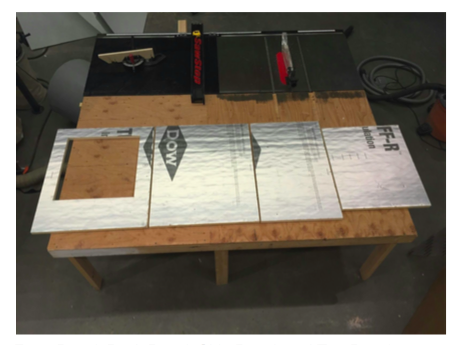
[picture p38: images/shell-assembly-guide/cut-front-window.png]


Front Panel, Back Panel, Side Panel, and Top Panel

## Gluing Together the Foam Box

*Follow the video and consult the CAD for better visuals on how to assemble the box*

Using hot glue, lay down a continuous zigzagging line about an inch wide along one of the edges to be glued.

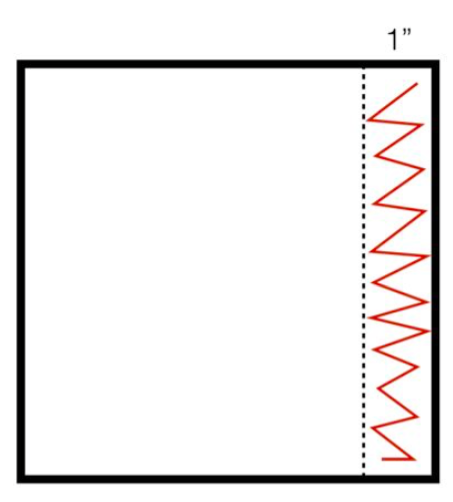
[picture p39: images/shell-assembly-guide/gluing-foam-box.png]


Firmly push the mating panels together and hold while the glue dries. The front and back panels should be on the outermost face, while the side panel sits between the front and back panels. The top panel should be placed on the top of the front, side, and back panels.

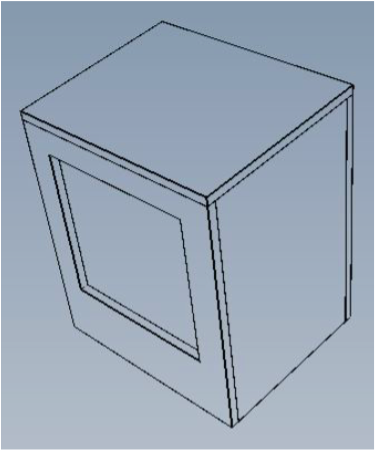
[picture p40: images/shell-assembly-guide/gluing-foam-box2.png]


## Taping the Edges

Once the box has been glued together, the exposed edges where the yellow insulation foam can be seen need to be covered up. Using foil tape, cover all exposed edges so that no foam can be seen.

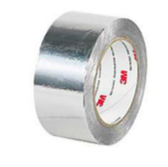
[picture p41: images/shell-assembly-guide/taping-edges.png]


## Cutting the Corruplast

Because the panel dimensions of the corruplast are larger than the foam, cutting approximate dimensions is not possible. In fact, the width dimensions of the panels add up perfectly to 8’ or 96”. So cutting along the exact lines is the only way to make use of the whole panel. Note, due to the width of the saw blade, each panel will be missing between 1/16” ­ 1⁄8” of material. This has not been a problem for us though.

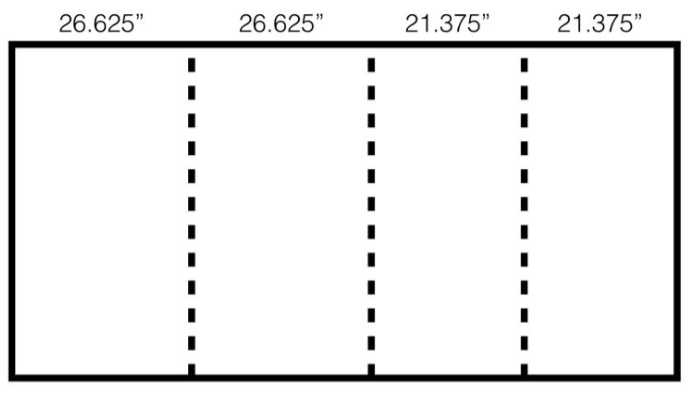
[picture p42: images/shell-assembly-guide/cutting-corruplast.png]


The exact dimensions are as follows:

```
Front Panel: 26.625” x 32.5625”
Back Panel: 26.625” x 32.5625”
Side Panel: 21.375” x 32.5625”
Top Panel: 21.375” x 26.4375”
```

Like the foam, next you need to cut the window into the front panel. I created a jig for this as well but a ruler works just fine. From the upper left corner as the origin of a cartesian system, measure 3.5” in the +x direction and 3.875 in the ­y direction. This will be the upper left corner of the window. The dimensions of the window are 19.75” wide by 20.3125” tall. Cut out the window and discard the scrap.

## Gluing the Corruplast to the Foam Box

We make use of Loctite spray adhesive with the web spray nozzle feature to get good coverage.



The directions on the bottle specify that each component get two coats of adhesive, spaced about 2­5min apart. The general procedure involved applying a coats of adhesive to both the corruplast and foam then carefully sticking the corruplast panels onto the foam box.

Refer to the CAD model and video to see orientation of the corruplast sheets and procedure of gluing. There will be a lip left on the bottom left side edges of the foam box. This is so that corruplast covers the PVC sheets for aesthetic purposes. When applying adhesive, be careful not to get too close to the hanging edge. The glue dries non­tacky so it isn’t much of a problem if a little glue gets on these regions. For alignment purposes, see that the corruplast creates a ~.5” rim around the center window. This will be where weatherstripping goes.

## Cutting the Window Plate

Using a tablesaw, cut a sheet of 1⁄8” polycarbonate to 19.75” x 30.3125”. Round the edges with a wood file and set aside. This will be the window plate.

## Creating the Window Seal and Magnetic Connection

Using the double­sided high­bond foam tape, stack two of the 0.75” neodymium disk magnets and tape one stack on each of the corners of the window, and in the middle of each of the edges of the window. Make sure all the magnets are the same polarity facing outward.

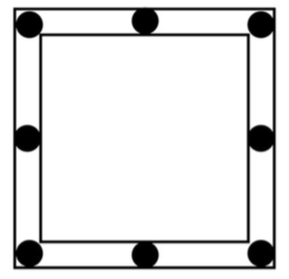
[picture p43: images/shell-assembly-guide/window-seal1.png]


Place strips of weatherstripping between the magnets in the .5” gap left by the corruplast.

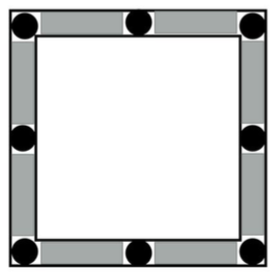
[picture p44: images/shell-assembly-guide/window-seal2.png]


Finally, foam tape magnets to the outside face of the window plate by aligning the window plate with the window in the shell, and placing the magnets over the stacks below.

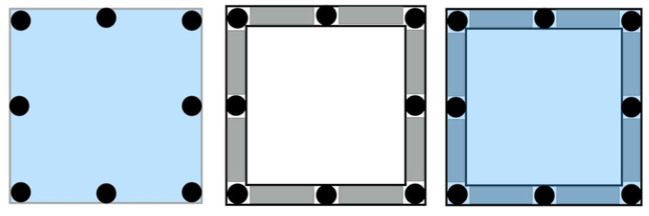
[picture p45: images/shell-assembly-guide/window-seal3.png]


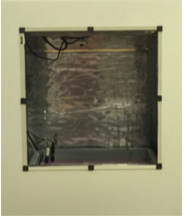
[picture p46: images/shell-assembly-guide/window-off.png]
Window Off


Window Off

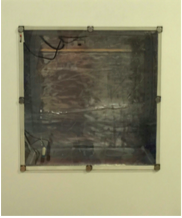
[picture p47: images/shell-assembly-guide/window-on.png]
Window On


Window On

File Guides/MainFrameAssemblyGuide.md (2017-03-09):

# Main Frame Assembly Guide

## Parts
  * PVC base board (32.875 in x 21.125 in)
  * PVC motherboard wall (31.875 in x 21.375 in)
  * 6 x 2” diameter PVC standoffs (Drill them yourself)
  * 6 x 2” self adhesive anti­skid surface pads Punched angle
    * 2 x 31 1⁄2” 4 x 30”
    * 4 x 24”
    * 7 x 18”
    * 4 x 6”
    * 2 x 1”
  * 26 x 3⁄8”­16 1” bolts
  * 46 x 3⁄8”­16 1⁄2” bolts 83 x 3⁄8”­16 nuts
  * 84 x 3⁄8” washers
  * 10’ weatherstrip tape

## Tools

  * 3⁄8” ratchet
  * 3⁄8” crescent wrench

## Instructions

1.   Place the PVC base board on a flat surface with the faux wood side down. The 6 holes on the left side outline the base of the electronics chamber, and the 10 holes on the right side outline the base of the grow chamber.

    

2.  Lay out 2 of the 6” punched angle lengths electronics side and 2 of the 24” punched angle lengths on the grow side as shown.

    

3.  Lay out 2 of the 18” punched angle lengths on the outermost sides of the base board and another on the right side of the electronics chamber side as shown. Secure this base frame with the 1” bolts on all non­corner through holes. Use washers on both sides of the board and put the heads of the bolts on the underside of the board.

    

4.  Place 1” bolts through 4 of the standoffs making sure the heads of the bolts are on the countersunk side of the standoffs.

    

5.  Insert these standoffs through the 4 outermost corner holes of the base board with the standoffs on the underside of the base board. Do not use washers on either side of the bolt. Make sure the bottom of your base board matches the picture below.

    

6.  Set the PVC motherboard wall on the table with the faux wood side down. Place 2 of the 30” punched angle lengths along the length of the board. Use 1” bolts with washers on each side to secure the 30” lengths to the board through the 4 aligning non­corner through holes. Orient the bolts such that heads are on the punched angle side of the wall.

    

7.  Place 1 of the 18” punched angle lengths along the top of the motherboard wall and use a 1” bolt to secure the 18” length at its center through the PVC motherboard wall.

    

8.  Now align the motherboard wall perpendicular to the base board, with the punched angle parts secured to the motherboard wall facing the grow chamber side as shown. Place 1 more of the 18” punched angle lengths at the base of the motherboard wall on the grow chamber side. Secure the 18” length to the motherboard wall and 18” length on the other side using 1” bolts with no washers at the two bottom corners and single center through hole. Orient the bolts such that heads are on the grow side of the motherboard wall.

    

9.  Set the frame on its side to insert the last standoffs and 1” bolts through the base board such that the bottom looks as shown. For the last 2 standoffs, do not use washers. For the rest, use washers only on the bottom of the base board. Tighten all bolts and standoffs with the ratchet and crescent wrench.

    

10.   Peel the paper off the backs of the 6 anti­skid pads and stick them to the standoffs as shown.

    

11.   Put the 1” angle brackets on the bolt ends on the electronics side of the motherboard wall. Orient the brackets as shown below. Secure each end with 1” bolts and no washers.

    

12.   Use the 2 30 1⁄2” punched angle lengths as the vertical posts on the outermost electronics chamber side, making sure that the end of the length with the cut through a punched hole is towards the top. Use the 1⁄2” bolts to secure the bases, with washers on the outside but not the inside of the punched angle corners. Make sure the intersections between angle parts are approximately perpendicular.

    

13.   Use the last 2 30” punched angle lengths for the outermost vertical posts on the grow chamber side of the frame. Again, use 1⁄2” bolts with washers on the outside and not the inside of the punched angle corners. Make sure the intersections between angle parts are approximately perpendicular.

    

    

14.   Install the top 18” angle part depths on the farthest left and right sides of the assembly with the 1⁄2” bolts with washers on the outside head sides of the bolts. Install the top 6” widths on the electronics chamber side, securing the two outer corners with 1⁄2” bolts with washers on the top side.

    

15.   Place the grow side top width 24” angle parts, making sure they are placed above the 18” top depth parts but inside the vertical posts.

    

16.   Get a top­down view of the assembly now, by either standing on the table or bringing the assembly down onto the floor. Secure the 6 corners with the last 1⁄2” bolts, with heads and washers on the top of the frame and nuts without washers on the underside.

17.   Do some last adjusting if the frame is crooked. Check each corner to make sure all pairs of angle bracket are perpendicular to each other. You may have to do some loosening and retightening of bolts.

18.   Now to make the seal between the main frame and jacket. Take your weatherstripping and line the base of the PVC base board on the grow side with it. Make sure the edge of the weatherstripping is right along the edge of the base but not protruding over the edge as this will make sliding the clam shell jacket over difficult or impossible. Do the same along the edge of the grow side of the PVC motherboard wall.

    

19.   Now, weatherstrip around the edge of the PVC motherboard wall cutout on the electronics chamber side. This will act as the seal when the electronics panel is pressed against the weatherstripping and bolted onto the motherboard wall.

    

20.   Take the laser cut front upper plate and back plate and install onto front and back faces of the punched angle frame on the electronics side, respectively. Use the 1⁄2” bolts and washers on the outer face and just nuts on the inner face.

    

21.   Find 20 of the magnets and put VHB tape onto one side, making sure the polarity orientation is the same for all 20. Tape 4 of the magnets along the punched angle that outlines the place of the front lower plate and 6 of the magnets along the punched angle that outlines the place of the side plate.

22.   Put the front lower plate against the punched angle, and align another set of magnets with those taped directly to the punched angle. Tape the new magnets onto the front lower plate.

    

23.   Do the same with the last 6 magnets and the side plate.

## Assemble the kit section

This is the “wet lab” section that sits underneath the electronics motherboard. It contains the materials for water chemistry balancing and managing a yeast reactor and also includes some safety equipment.



Yeast reactor: Drill a 3⁄8” hole in the lid of the bioreactor bottle. Hot glue the one­way valve into the opening, making sure that the arrow on the valve is pointing upwards, out of the bottle. Cut 2’ of the 3⁄8” tubing and push one end onto the one­way valve and route the other through the bottom left hole in the electronics panel through to the grow chamber side. The bottle behind the yeast reactor is filled with sugar.

To the right of the yeast reactor bottle are the four fertilizer bottles. Two contain dry fertilizer while the other two contain solutions of the fertilizers in water. Behind those fertilizer bottles sits the pH balancing kit.

Not seen behind the box of gloves are extra packets of yeast, measuring spoons, safety glasses, and pipettes.

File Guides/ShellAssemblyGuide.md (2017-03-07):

# Shell Assembly Guide

## Cutting the Insulation Foam

If you are cutting using a standard table saw, I found that it is easier to cut the large 4’x8’ sheet into sections slightly larger than the ultimate panel dimensions. This both makes each individual panel easier to work with and provides a clean opposite to the final cut width.



Once the sheets have been cut into the approximate panel dimensions, you can then cut the actual dimensions in the CAD.

```
Front Panel: 25.6875” x 30.625”
Back Panel: 25.6875” x 30.625”
Side Panel: 19.375” x 30.625”
Top Panel: 21.375” x 25.6875”
```

Next you need to cut the window into the front panel. I created a jig but a ruler works just fine. From the upper left corner as the origin of a cartesian system, measure 3.25” in the +x direction and 3.1875 in the ­y direction. This will be the upper left corner of the window. The dimensions of the window are 18.75” wide by 19.3125” tall. See picture below for relative orientation if confused. Cut out the window and discard the scrap.



Front Panel, Back Panel, Side Panel, and Top Panel

## Gluing Together the Foam Box

*Follow the video and consult the CAD for better visuals on how to assemble the box*

Using hot glue, lay down a continuous zigzagging line about an inch wide along one of the edges to be glued.



Firmly push the mating panels together and hold while the glue dries. The front and back panels should be on the outermost face, while the side panel sits between the front and back panels. The top panel should be placed on the top of the front, side, and back panels.



## Taping the Edges

Once the box has been glued together, the exposed edges where the yellow insulation foam can be seen need to be covered up. Using foil tape, cover all exposed edges so that no foam can be seen.



## Cutting the Corruplast

Because the panel dimensions of the corruplast are larger than the foam, cutting approximate dimensions is not possible. In fact, the width dimensions of the panels add up perfectly to 8’ or 96”. So cutting along the exact lines is the only way to make use of the whole panel. Note, due to the width of the saw blade, each panel will be missing between 1/16” ­ 1⁄8” of material. This has not been a problem for us though.



The exact dimensions are as follows:

```
Front Panel: 26.625” x 32.5625”
Back Panel: 26.625” x 32.5625”
Side Panel: 21.375” x 32.5625”
Top Panel: 21.375” x 26.4375”
```

Like the foam, next you need to cut the window into the front panel. I created a jig for this as well but a ruler works just fine. From the upper left corner as the origin of a cartesian system, measure 3.5” in the +x direction and 3.875 in the ­y direction. This will be the upper left corner of the window. The dimensions of the window are 19.75” wide by 20.3125” tall. Cut out the window and discard the scrap.

## Gluing the Corruplast to the Foam Box

We make use of Loctite spray adhesive with the web spray nozzle feature to get good coverage.



The directions on the bottle specify that each component get two coats of adhesive, spaced about 2­5min apart. The general procedure involved applying a coats of adhesive to both the corruplast and foam then carefully sticking the corruplast panels onto the foam box.

Refer to the CAD model and video to see orientation of the corruplast sheets and procedure of gluing. There will be a lip left on the bottom left side edges of the foam box. This is so that corruplast covers the PVC sheets for aesthetic purposes. When applying adhesive, be careful not to get too close to the hanging edge. The glue dries non­tacky so it isn’t much of a problem if a little glue gets on these regions. For alignment purposes, see that the corruplast creates a ~.5” rim around the center window. This will be where weatherstripping goes.

## Cutting the Window Plate

Using a tablesaw, cut a sheet of 1⁄8” polycarbonate to 19.75” x 30.3125”. Round the edges with a wood file and set aside. This will be the window plate.

## Creating the Window Seal and Magnetic Connection

Using the double­sided high­bond foam tape, stack two of the 0.75” neodymium disk magnets and tape one stack on each of the corners of the window, and in the middle of each of the edges of the window. Make sure all the magnets are the same polarity facing outward.



Place strips of weatherstripping between the magnets in the .5” gap left by the corruplast.



Finally, foam tape magnets to the outside face of the window plate by aligning the window plate with the window in the shell, and placing the magnets over the stacks below.



Window Off

Window Off

Window On

Window On

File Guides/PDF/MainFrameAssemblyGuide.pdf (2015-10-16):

Parts:

PVC base board
PVC motherboard wall
6 x 2” diameter PVC standoffs
6 x 2” self adhesive antiskid surface pads Punched angle
2 x 31 ½”
4 x 30”
4 x 24”
7 x 18”
4 x 6”
2 x 1”
26 x ⅜”-16 1” bolts
46 x ⅜”-16 ½” bolts
83 x ⅜”-16 nuts
84 x ⅜” washers
10’ weatherstrip tape

Tools:

⅜” ratchet
⅜” crescent wrench

Instructions:

1. Place the PVC base board on a flat surface with the faux wood side down. The 6 holes on the left side outline the base of the electronics chamber, and the 10 holes on the right side outline the base of the grow chamber.

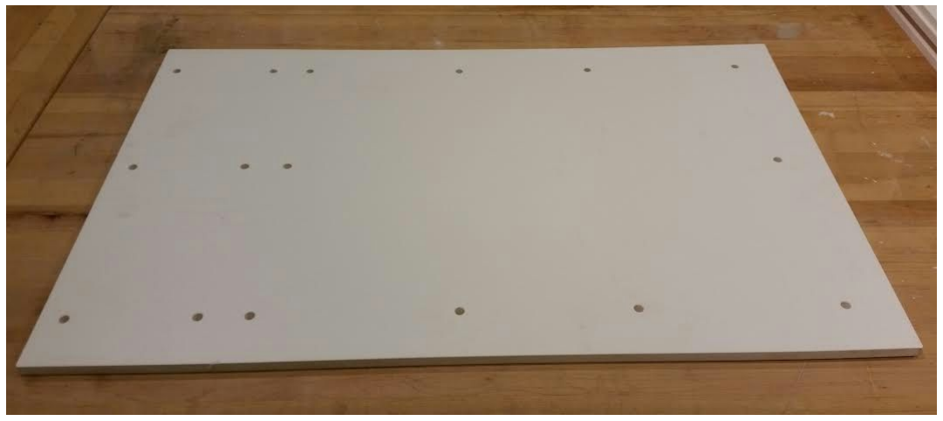
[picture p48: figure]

2. Lay out 2 of the 6” punched angle lengths electronics side and 2 of the 24” punched angle lengths on the grow side as shown.

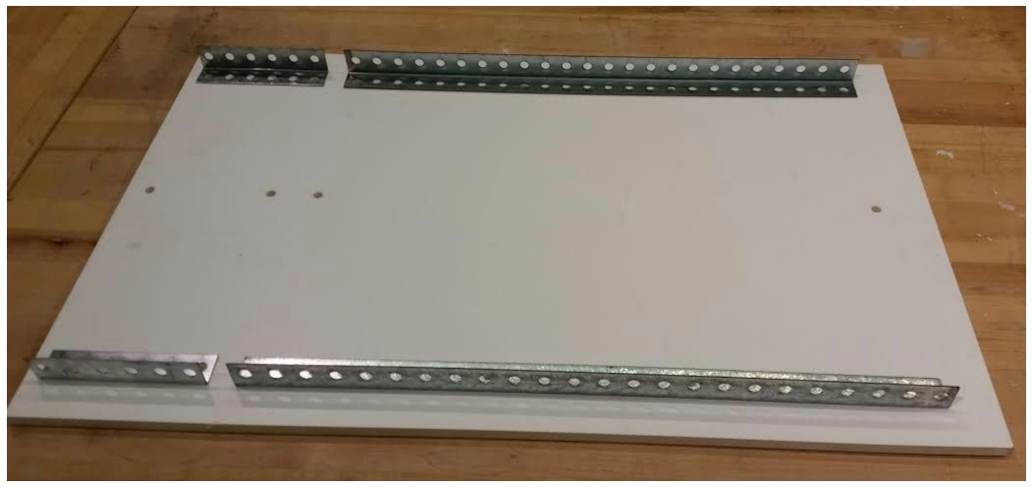
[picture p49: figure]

3. Lay out 2 of the 18” punched angle lengths on the outermost sides of the base board and another on the right side of the electronics chamber side as shown. Secure this base frame with the 1” bolts on all noncorner through holes. Use washers on both sides of the board and put the heads of the bolts on the underside of the board.

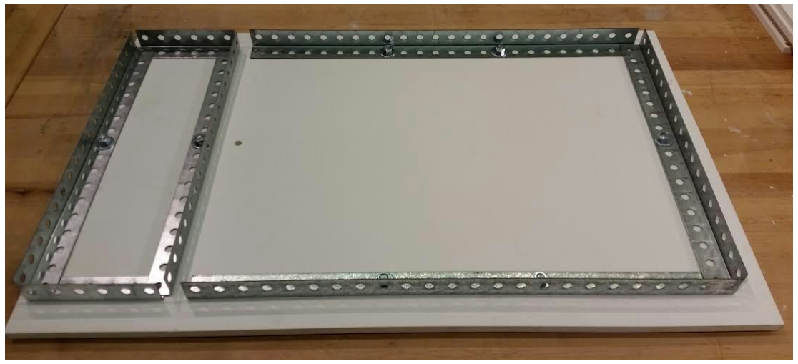
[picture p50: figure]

4. Place 1” bolts through 4 of the standoffs making sure the heads of the bolts are on the countersunk side of the standoffs.

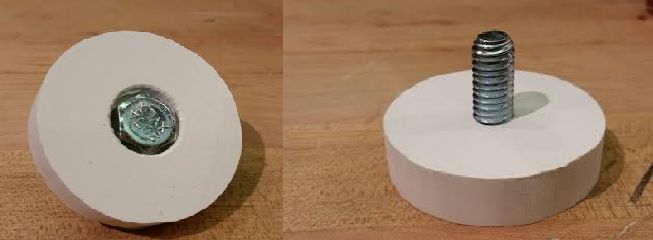
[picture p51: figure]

5. Insert these standoffs through the 4 outermost corner holes of the base board with the standoffs on the underside of the base board. Do not use washers on either side of the bolt. Make sure the bottom of your base board matches the picture below.

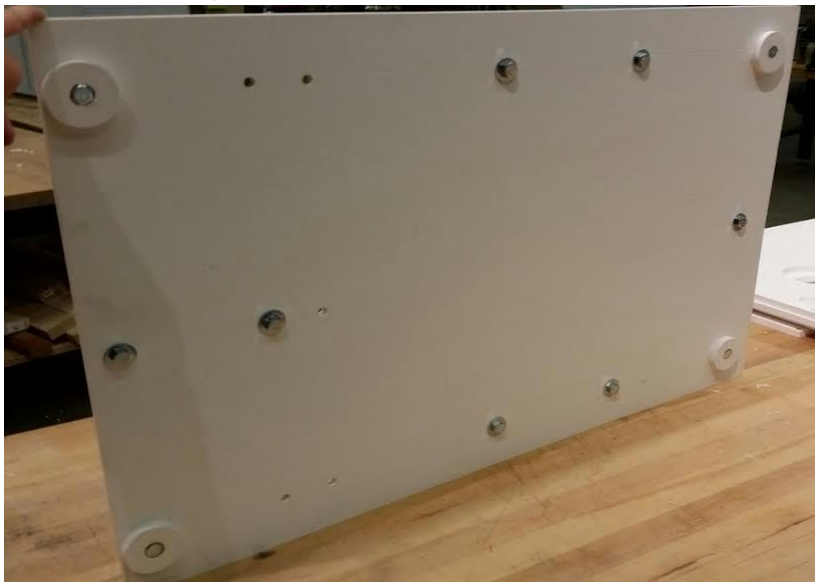
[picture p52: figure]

6. Set the PVC motherboard wall on the table with the faux wood side down. Place 2 of the 30” punched angle lengths along the length of the board. Use 1” bolts with washers on each side to secure the 30” lengths to the board through the 4 aligning noncorner through holes. Orient the bolts such that heads are on the punched angle side of the wall.

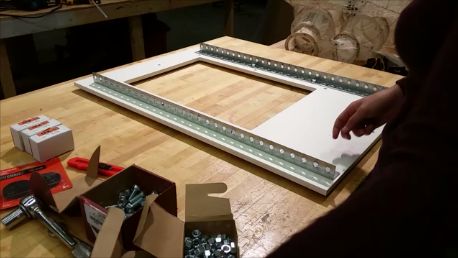
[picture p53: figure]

7. Place 1 of the 18” punched angle lengths along the top of the motherboard wall and use a 1” bolt to secure the 18” length at its center through the PVC motherboard wall.

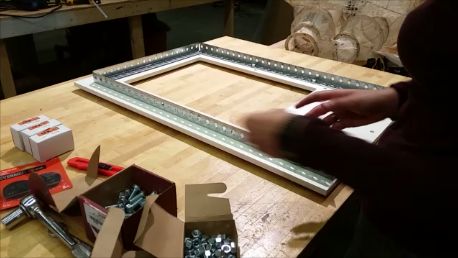
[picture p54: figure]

8. Now align the motherboard wall perpendicular to the base board, with the punched angle parts secured to the motherboard wall facing the grow chamber side as shown. Place 1 more of the 18” punched angle lengths at the base of the motherboard wall on the grow chamber side. Secure the 18” length to the motherboard wall and 18” length on the other side using 1” bolts with no washers at the two bottom corners and single center through hole. Orient the bolts such that heads are on the grow side of the motherboard wall.

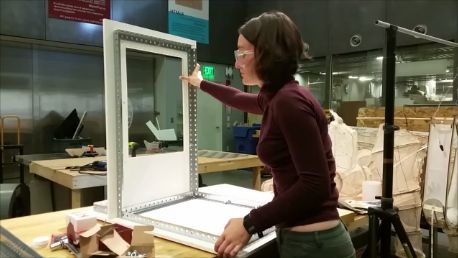
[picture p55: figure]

9. Set the frame on its side to insert the last standoffs and 1” bolts through the base board such that the bottom looks as shown. For the last 2 standoffs, do not use washers. For the rest, use washers only on the bottom of the base board. Tighten all bolts and standoffs with the ratchet and crescent wrench.


10. Peel the paper off the backs of the 6 antiskid pads and stick them to the standoffs as shown.


11. Put the 1” angle brackets on the bolt ends on the electronics side of the motherboard wall. Orient the brackets as shown below. Secure each end with 1” bolts and no washers.
12. Use the 2 30 ½” punched angle lengths as the vertical posts on the outermost electronics chamber side, making sure that the end of the length with the cut through a punched hole is towards the top. Use the ½” bolts to secure the bases, with washers on the outside but not the inside of the punched angle corners. Make sure the intersections between angle parts are approximately perpendicular.


13. Use the last 2 30” punched angle lengths for the outermost vertical posts on the grow chamber side of the frame. Again, use ½” bolts with washers on the outside and not the inside of the punched angle corners. Make sure the intersections between angle parts are approximately perpendicular.


14. Install the top 18” angle part depths on the farthest left and right sides of the assembly with the ½” bolts with washers on the outside head sides of the bolts. Install the top 6” widths on the electronics chamber side, securing the two outer corners with ½” bolts with washers on the top side.
15. Place the grow side top width 24” angle parts, making sure they are placed above the 18” top depth parts but inside the vertical posts.


16. Get a topdown view of the assembly now, by either standing on the table or bringing the assembly down onto the floor. Secure the 6 corners with the last ½” bolts, with heads and washers on the top of the frame and nuts without washers on the underside.
17. Do some last adjusting if the frame is crooked. Check each corner to make sure all pairs of angle bracket are perpendicular to each other. You may have to do some loosening and retightening of bolts.
18. Now to make the seal between the main frame and jacket. Take your weatherstripping and line the base of the PVC base board on the grow side with it. Make sure the edge of the weatherstripping is right along the edge of the base but not protruding over the edge as this will make sliding the clam shell jacket over difficult or impossible. Do the same along the edge of the grow side of the PVC motherboard wall.


19. Now, weatherstrip around the edge of the PVC motherboard wall cutout on the electronics chamber side. This will act as the seal when the electronics panel is pressed against the weatherstripping and bolted onto the motherboard wall.


20. Take the laser cut front upper plate and back plate and install onto front and back faces of the punched angle frame on the electronics side, respectively. Use the ½” bolts and washers on the outer face and just nuts on the inner face.


21. Find 20 of the magnets and put VHB tape onto one side, making sure the polarity orientation is the same for all 20. Tape 4 of the magnets along the punched angle that outlines the place of the front lower plate and 6 of the magnets along the punched angle that outlines the place of the side plate.
22. Put the front lower plate against the punched angle, and align another set of magnets with those taped directly to the punched angle. Tape the new magnets onto the front lower plate.


23. Do the same with the last 6 magnets and the side plate.

Assemble the kit section.

This is the “wet lab” section that sits underneath the electronics motherboard. It contains the materials for water chemistry balancing and managing a yeast reactor and also includes some safety equipment.


Yeast reactor: Drill a ⅜” hole in the lid of the bioreactor bottle. Hot glue the oneway valve into the opening, making sure that the arrow on the valve is pointing upwards, out of the bottle. Cut 2’ of the ⅜” tubing and push one end onto the oneway valve and route the other through the bottom left hole in the electronics panel through to the grow chamber side. The bottle behind the yeast reactor is filled with sugar.

To the right of the yeast reactor bottle are the four fertilizer bottles. Two contain dry fertilizer while the other two contain solutions of the fertilizers in water. Behind those fertilizer bottles sits the pH balancing kit.

Not seen behind the box of gloves are extra packets of yeast, measuring spoons, safety glasses, and pipettes.

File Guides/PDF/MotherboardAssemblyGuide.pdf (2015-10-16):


Plant side of electronics panel


User side of electronics panel


(a larger zoomable copy of this schematic is in the documentation)

*Assembling the electronics panel is tricky but manageable, you just have to consult two or three of the diagrams at once. The pictures of position give an indication of where the components are placed on the panel. The schematic gives real wiring/polarity directions for assembling the subcomponents. Soldering will be required to join some wires.

1. 120VAC Control Module
a. Materials

i. 2-gang box bottom
ii. | 2-gang box top
iii. | 2-channel AC socket x2
iv. | 4-channel relay
v. Female jumpertogrove cable x2
vi. | 6-channel, maletofemale jumper wire
vii. | 6 foot, 3-prong extension cable
viii. | 3-port, Wago, lever connector x2
ix. | 5-port, Wago, lever connector
x. 0.5” screw x4
b. Tools
i. Medium, phillips screwdriver
ii. | Wire strippers
iii. | Hot glue gun
iv. | Hammer
c. Tools Consumables
i. Hot glue
ii. | Electrical Tape
iii. | Duct tape
iv. | Permanent Marker
d. Instructions
i. Create shortened AC connector (10” total length, male).
1. Cut the extension cord 8” away from the base of the male side of
| the cable. The total cable length will be approximately 10”.
2. Strip off approximately 2” of the outer encasement from the cable.
3. Strip off approximately ½” of insulation from each of the three
| wires that are now exposed.
ii. | Tap out a center tab from the 2-gang box bottom
iii. | Feed the exposed wire end on the extension cable through this hole and
| connect to the wago lever connectors. IMPORTANT:you must put the
| extension cable through the hole beforeattaching the connectors
| otherwise the cable will not fit through later in the assembly.
1. Connect the black wire (hot) to a 5-port connector
2. Connect the white wire (neutral) to a 3-port connector
3. Connect the green wire (ground) to a separate 3-port connector iv. Create intermediary AC wires (6” segments x6 BLK, x3 GRN, x3 WHT)
1. Using the remains of the extension cable cut x6 6” segments and
| pull out all the wires from the encasement.
2. Strip each wire such that there is approximately 1” of exposed wire
| on one end and ½” of exposed wire on the other end. Create x6
| black wires, x3 green wires, and x3 white wires.
v. Create x2 modified AC sockets

1. Break off the tab connecting the “hot” screw terminals.The “hot” screw terminals have gold screws and are labeled “hot” on the back of the sockets. Note: this tab is located in between the screw terminals and is a very small lip that is the same gold color as the plating around it.
2. Using the permanent marker, label the top plug on one of the sockets “1” and the bottom plug “2”. Do the same on the other socket, however, label them “3” and “4”.
3. Bend the protruding mounting tabs that are located on the top and bottom of the socket so they form 90 degree angles and are able to fit into the 2-gang box
4. Connect the 1” end of a black wires to each “hot” screw terminal on the socket. Remember: the “hot” terminals have the golden screws and are labeled on the backside of the socket. You will connect two black wires per socket.
5. Connect the 1” end of a white wire to either of the neutral screw terminals on the socket. These terminals have silver screws and are also labeled on the back of the socket.
6. Connect the 1” end of a green wire to the ground screw terminal on the socket. The ground screw terminal is green.
vi. | Connect the ground and common from both AC sockets to the Wago
| 3-port lever connectors containing the ground and common from the
| extension cable, respectively.
vii. | Connect the AC sockets to the relay block.
1. Connect the black wire (“hot”) from the socket labeled “1” to the
| middle screw terminal labeled K1 on the relay block. Do this for
| sockets 2,3,4 connecting to K2, K3, and K4 respectively.
2. When viewing the screw terminals on the relay block head on,
| connect x4 black wires to the left terminal in each of K# block.
3. Connect all 4 of the black wires connected to the left terminal on
| the relay block to the Wago 5-port lever connector containing the
| black wire from the extension cable.
viii. | Screw the sockets to the 2-gang box top such that the 1-2 socket is on
| the left and the 3-4 socket is on the right.
ix. | Connect control cables to the relay block
1. Connect the 6-channel, maletofemale jumper cables to the 6
| exposed header pins on the relay block
2. To keep headers securely fastened, squirt a hefty amount of hot
| glue around the connection.
3. Using a single female jumpertogrove cable, connect the black
| wire on the grove cable to the wire attached to GND on the
| relay,the whitewire on the grove cable to the wire attached to IN1
| on the relay, the yellowwire on the grove cable to the wire

attached to IN2 on the relay. This cable will connect to the D8 receptacle on the arduino grove shield so it is recommended you use the permanent marker to label the end of the connector “D8”.
4. Using the other female jumpertogrove cable, connect the red wire on the grove cable to the wire attached to VCC on the relay,the whitewire on the grove cable to the wire attached to IN3 on the relay, the yellowwire on the grove cable to the wire attached to IN4 on the relay. This cable will connect to the D6 receptacle on the arduino grove shield so it is recommended you use the permanent marker to label the end of the connector “D6”.
5. For each cable, hot glue the connection between the maletofemale jumper cable and the female jumpertogrove cable and then wrap the connection in electrical tape once the hot glue dries
6. Route these cables out of the box from the same hole that was knocked out to insert the extension cable.
x. Insulate the bottom of the relay block
1. Place a layer of electrical tape on the bottom of the relay block
2. Place a layer of duct tape over the layer of electrical tape on the bottom of the relay block
xi. | Using the small screws, attach this module to the motherboard on top of
| the footprint labeled “AC”
xii. | Screw in the top of the 2-gang box
xiii. | Once the wire management module is built, the extension cable will plug
| into the power strip.
xiv. | Test the device by plugging in something to each AC port. Use 5V and
| the ground pin of an Arduino to power and activate each relay channel on
| the relay block.
2. 12V-30A Power Supply Module
a. Materials
i. 12V-30A power supply
ii. | 6 foot, 3-prong extension cable
iii. | 4-pin, buckled, 50cm grove cable
iv. | 14” x 1” mounting tape
b. Tools
i. Medium, phillips screwdriver
ii. | Wire strippers
iii. | Tape measure
iv. | Multimeter
c. Instructions
i. Create shortened AC connector (10” total length, male).

1. Cut the extension cord 8” away from the base of the male side of the cable. The total cable length will be approximately 10”.
2. Strip off approximately 2” of the outer encasement from the cable.
3. Strip off approximately 1” of insulation from each of the three wires that are now exposed.
ii. | Connect shortened AC connector to power supply (BLK-L, WHT-N,
| GRN-GND)
1. Connect the black wire (hot) from the shortened ac connector to
| the screw terminal on the power supply with the “L”symbol
| overhead. Note: a better connection is made by placing the wires
| on the left hand side of the screw so that when the screw is
| tightened (turned to the right), the wire stays within the receptacle.
2. Connect the white wire (neutral) from the shortened ac connector
| to the screw terminal on the power supply with the “N”symbol
| overhead.
3. Connect the green wire (ground) from the shortened ac connector
| to the screw terminal on the power supply with the “GND”symbol
| overhead. Note: the GND, or ground, symbol is the the symbol
| with multiple horizontal lines.
iii. | Create modified grove cable
1. Cut off one side of the grove cable very close to the base. Either
| side will work.
2. Strip off approximately 1” of insulation from the red and black
| wires. Do nothing with the white and yellow wires.
iv. | Connect modified grove cable to the power supply
1. Connect the blackwire from the grove cable to one of the -V
| screw terminals on the power supply.
2. Connect the redwire from the grove cable to one of the +Vscrew
| terminals on the power supply.
v. Tune power supply so it outputs exactly 12V
1. Use the multimeter to probe the +V and -V terminals on the power
| supply. Using the adjustment screw, tune the output voltage to be
| as close to 12V as possible.
vi. | Apply 2 strips of approximately 7” strips of mounting tape to the underside
| of the power supply and place it nearly flush against the AC control
| module. The bottom of the power supply should be tangent with the
| bottom of the AC relay box leaving approximately ¼” gap between the two
| verticals.
vii. | Once the wire management module is built, the AC extension cablewill
| plug into the power strip.
viii. | Once the arduino protoshield module is built, the grove connectorwill
| plug into S4.

### 3. Air Exchanger Module

a. Materials
i. Heater
ii. | 7” x 7” x 5” project box
iii. | USB-to-AC converter
iv. | 6” Fans x2
v. 6” Fan Guards x3
vi. | 4” Louvre
vii. | Humidifier
viii. | 6” x ½” weather stripping
ix. | Air pump
x. Air stone
xi. | 24” of .125” inner diameter tubing
xii. | Small (.5”) screws x4
xiii. | Medium (1”) screws x4
xiv. | Long screws (1.5”) x4
xv. | Standoffs (can just use bolts from frame) x4
b. Tools
i. Power Drill
ii. | 1 ¾” hole saw drill bit
iii. | 4 ½” hole saw drill bit
iv. | 12” x 1” mounting tape
v. Hand file
c. Instructions
i. Create modified project box.
1. A few tips before starting. First mark all holes on the box. Check
| they are in the correct positions. When drilling each hole, drill pilot
| holes first. Then, create groove by running hole saw bit in reverse
| direction. Finish cut by running hole saw bit in forward direction.
| For the large hole saw bit you may need to do the entire cut by
| running the bit in the reverse direction. After cuts are made, clean
| up edges with a file.
2. When viewed from the back of the box, drill a 4 ½” diameter hole
| that is centered 2 ⅜” right and 2 ⅜” up from the bottom left corner.
3. When viewed from the back of the box, drill a 1 ¾” diameter hole
| that is centered 1” left and 2 ⅜” up from the bottom right corner.
4. When viewed from the right of the box (from the front of the box),
| drill a 1 ¾” diameter hole that is centered 1 ½” left and 1 ½” down
| from the top right corner of the box.
ii. | Mount heater into modified project box
1. When looking into the project box with the big hole on the right
| and the little hole on the left the heater will be mounted upside
| down with the front of the heater oriented through the big hole.

The heater will be pushed all the way into the bottom right corner of the box.
2. Make sure the heater is switched ON. Route the heater able through the right side hole then apply mounting tape to the all sides of the heater that will be in contact with the project box. iii. Attach project box to the motherboard
1. Place the modified project box with the heater inside of it onto the
| motherboard on the section labeled “air XC”.
2. Secure the box by screwing x4 small screws into the corners. Seal
| the project box cover. Drop the screws into the holes and use a
| screwdriver to drive them into the PVC.
iv. | Assemble and mount the air pump on top of the air exchange box
1. Push one end of the tubing onto the end of the air pump. Route
| this line down the left side of the motherboard and pop the tube
| through the hole on the lower left side of the panel.
2. The power cord from the air pump will go into the wire
| management module and plug in directly to the power stip. The air
| pump will therefore always be running when the power is on.
3. Hot glue the feet of the pump so that the pump does not fall off the
| air exchange box when the motherboard panel is jostled. Mount
| the air pump as far from the wall as possible because wires will
| have to be able to make it through that hole.
v. Assemble and mount the vent fan
1. Place one of the fans on top of the lower large hole of the
| motherboard panel such that the air is blowing into the grow
| chamber. There is a graphic on a side of the fan with arrows that
| indicate which direction the fan blows air as well as which direction
| the fan spins.
2. Place a fan guard over top of the fan such that it is on the surface
| furthest from the inside of the grow chamber.
3. Using x4 of the medium sized screws, mount the fan to the
| motherboard.
vi. | Assemble and mount the louvre
1. The inner cylinder on the louvre protrudes too far into the opening
| of the motherboard. Shorten the cylinder with an exacto knife by at
| least half its length.
2. The louvre will be mounted on the inside of the motherboard, on
| the surface inside the grow chamber. Make sure the louvre is
| oriented such that gravity keeps them closed.
3. Using x4 of the small sized screws, mount the louvre to the
| motherboard.
vii. | Assemble and mount the circulation fan

1. Mount the circulation fan on the inside of the electronics panel in the lowest possible position that is closest to the front of the bot. Make sure the fan is oriented such that it is blowing into the chamber. In order to generate airflow, standoffs (3 washers) must be placed in between the fan and the motherboard. Also for safety, place a fan guard on the surface furthest into the grow chamber. Use the long screws to attach to the motherboard. For clarity, the order of materials is: inside of motherboard, standoffs, fan, fan guard, long screws running through to hold it all together.
2. The circulation and vent fan will be wired together. Consult the schematic for polarity. Each fan has a three channel cable. The gold cable is ground, and the center cable is power (12V). The third cable is not used. Taking a grove cable, connect red and black to the circulation fan power and ground, and white and yellow to the power and ground of the vent fan. The connector end of the grove cable will then plug into S2.
viii. Assemble and mount the humidifier
1. The humidifier mount bracket is created from a 6” long section of
| stamped angle. First, a notch is cut down the spine of the angle
| about 1” in length with a bandsaw. Next, using a metal brake,
| each side of the angle is flared out at the 1” mark to create a tab
| perpendicular to the main length of slotted angle. Finally, bolt a 1”
| section of stamped angle to the end of the bracket to prevent the
| humidifier from slipping out.


2. Drill holes for humidifier, diameter 1 ¾” 4” from right side and 2 3/4” from bottom (when looking at grow chamber side). Drill two 5/16” humidifier mount holes 1 ¾” apart and 2” below the center of the humidifier hole. The bracket will help with alignment. Using a ⅜-16 tap, thread the 5/16” holes.
3. Bolt in the humidifier mount to the board.

4. Apply weather stripping to the lower top surface of the humidifier. The part that will sit against the motherboard. NOT the part that will protrude through it.
5. When the humidifier is pressed up against the motherboard, make sure that the usb port is facing directly to the right. With the usb port facing to the right, carefully take off the plastic encasement of the wick. Note how this encasement fits back onto the humidifier. Using a heat source, either a heat gun, lighter, or something equivalent, slowly head the center of the encasement and slowly bend the piece down. The entire purpose of doing this is so that the wick can suck up water when the humidifier is placed in a horizontal position so make sure the way you bent the wick complies with this goal as well as orienting the usb port to the right.
6. Press fit the modified humidifier into the mount and connect the usb port. Route the cable through the wire management unit and plug it into the USB-to-AC converter. Plug in the converter to the AC Control module in port 2.

### 4. Wire Management Module

a. Materials
i. Wire management box
ii. | 6-channel power strip
iii. | 34” x 1” mounting tape
b. Tools
i. Power drill
ii. | .5” diameter drill bit
iii. | 1.5” hole saw bit
c. Instructions
i. Viewed from the right side of the wire management box, drill a 1/2”
| diameter hole centered 1” down and ¼” to the left from the upper right
| corner of the box and such that the bottom of the hole is flush with the
| motherboard. This hole will accommodate the USB port on the arduino,
| so you gauge position necessary by the height the arduino sits above the
| motherboard.
ii. | Viewed from the right side of the wire management box, drill a 1.5”
| diameter hole centered 1 1/2” down and 2” to the left from the upper right
| corner of the box.
iii. | Viewed from the right side of the wire management box, drill a 1.5”
| diameter hole centered 6” down and 1/2” left of the upper right corner of
| the box and such that the bottom of the hole is flush with the
| motherboard.


The two holes will provide cable paths to the Arduino and for the water sensors

iv. | Viewed from the top of the wire management box, using a 10” strip of
| mounting tape to secure the power strip to the lower left corner of the
| inside of the box such that the trailing power cable will protrude towards
| the top of the motherboard.
v. Using 2 strips of 12” segments of mounting tape, attach the top of the wire
| management module flush with the top of the air exchange box and
| 12V-30A power supply. There should be approximately 1” gap between
| the top of the AC control module and the bottom of the wire management
| module.

### 5. DC Control Module

a. Materials
i. 4-channel relay block
ii. | Female jumpertogrove cable x2
iii. | 4-pin, buckled, 10cm grove cable
iv. | 6-channel, maletofemale jumper wire
v. small .5” screws x4
b. Tools
i. Wire strippers
ii. Hot glue gun
c. Tools Consumables
i. Hot Glue
ii. Electrical Tape

iii. Permanent Marker
d. Instructions
i. Connect control cables to the relay block
1. Connect the 6-channel, maletofemale jumper cables to the 6
| exposed header pins on the relay block
2. To keep headers securely fastened, squirt a hefty amount of hot
| glue around the connection.
3. Using a single female jumpertogrove cable, connect the black
| wire on the grove cable to the wire attached to GND on the
| relay,the whitewire on the grove cable to the wire attached to IN1
| on the relay, the yellowwire on the grove cable to the wire
| attached to IN2 on the relay. This cable will connect to the S3
| receptacle on the arduino protoboard module so it is
| recommended you use the permanent marker to label the end of
| the connector “S3”.
4. Using the other female jumpertogrove cable, connect the red
| wire on the grove cable to the wire attached to VCC on the
| relay,the whitewire on the grove cable to the wire attached to IN3
| on the relay, the yellowwire on the grove cable to the wire
| attached to IN4 on the relay. This cable will connect to the S9
| receptacle on the arduino protoboard module so it is
| recommended you use the permanent marker to label the end of
| the connector “S9”.
5. For each cable, hot glue the connection between the
| maletofemale jumper cable and the female jumpertogrove
| cable and then wrap the connection in electrical tape once the hot
| glue dries.
ii. | Connect the switch cables to the relay block
1. Cut the 10cm grove cable into 2 segments. One segment ⅔ of the
| cable and the other ⅓.
2. Strip approximately ½” of insulation off the tips of each cable
3. On the longer cable, connect blackto the center port of the K1
| screw terminal (K1-SW). Connect redto the left port of the K1
| screw terminal (K1-ON). Left is defined by viewing the screw
| terminals from the front, or looking into the board. Connect white
| to the center port of the K2screw terminal (K2-SW).Connect
| yellowto the left port of the K2screw terminal (K2-ON). Left is
| defined by viewing the screw terminals from the front, or looking
| into the board. This cable will connect to the S1receptacle on the
| arduino protoboard module so it is recommended you use the
| permanent marker to label the end of the connector “S1”.
4. On the shorter cable, connect blackto the center port of the K3
| screw terminal (K3-SW). Connect redto the left port of the K3

screw terminal (K3-ON). Left is defined by viewing the screw terminals from the front, or looking into the board. Connect white to the center port of the K4screw terminal (K4-SW).Connect yellowto the left port of the K4screw terminal (K4-ON). Left is defined by viewing the screw terminals from the front, or looking into the board. This cable will connect to the S7receptacle on the arduino protoboard module so it is recommended you use the permanent marker to label the end of the connector “S7”.
iii. Insulate the bottom of the relay block
1. Place a layer of electrical tape on the bottom of the relay block
2. Place a layer of duct tape over the layer of electrical tape on the
| bottom of the relay block
iv. | Mount the relay block onto the motherboard
1. Using the small screws, mount the relay block to the segment on
| the board labeled “DC”

### 6. Water Sensors Module

a. Materials
i. EC and Water Temperature Sensor
ii. | pH Sensor
iii. | small .5” screws x6
iv. | Male jumpertogrove cable x3
b. Tools
i. Small, phillips screwdriver ii. Hot glue gun
c. Tools Consumables
i. Hot Glue
ii. Electrical Tape
d. Instructions
i. Build the temperature sensor module
1. Plug in the temperature sensor (the silver cylinder with a wire
| coming out of it) to the temperature sensor PCB. The yellowwire
| goes to the Aterminal, redwire to the Bterminal, and greywire to
| the Cterminal.
2. Plug in the small red, black and green cable into the temperature
| sensor PCB. Using a male jumpertogrove cable, connect the red
| grovewire to the red sensorwire, the black grovewire to the
| black sensor wire, and the yellowgrove wire to the green
| sensorwire.
3. This cable will connect to the D5receptacle on the arduino grove
| shield module so it is recommended you use the permanent
| marker to label the end of the connector “D5”.
ii. | Mount the temperature sensor module to the motherboard

1. Using two electronics screws, mount the temperature sensor to the two predrilled holes that sit directly to the left of the DC relay module. The module should be oriented such that the green, red, and black wires are towards the top of the motherboard.
2. Route all cables coming from the PCB through the lower drilled hole in the wire management module. Route the grove cable through the upper drilled hole in the wire management module. Route the sensor through the bottom slat in the wire management module and through the bottom hole leading into the grow chamber. Once the panel is connected to the chamber, snake the sensor into the corner of the water tray such that it is beneath the styrofoam grow tray.
iii. Build the EC sensor module
1. Like the temprature sensor, use two screws to mount the EC
| board directly below the DC relay module. Connect the
| corresponding EC probe and route through the center hole in the
| wire management box and route down and out the bottom hole to
| the grow chamber.
iv. Build the pH sensor module
1. Mount the pH board below the EC board and also connect and
| route the cable through the wire management box and down and
| out through the hole into the grow chamber.

### 7. Water Circulation Module

a. Materials
i. Foam tray with holes cut for the sensors and horticubes
ii. | 12” of .5” inner diameter tubing
iii. | Aquarium water pump
iv. | reservoir tub
b. Tools
i. Scissors
ii. ShopBot
c. Instructions
i. Use the ShopBot to cut the foam tray.
ii. | Place the aquarium pump in the reservoir tub and attach the tube to the
| outlet of the pump
iii. | Place the sensors through the holes in the foam tray so that the ends
| stick in the water. Make sure that the tips are always in liquid, either
| water or the solutions they came with.

### 8. Arduino Mega Protoshield Module

a. Materials
i. Protoshield package

ii. | Grove connector sockets x9
iii. | Wirewrapping wire assortment
b. Tools
i. Wire strippers
ii. | Soldering iron
iii. | Wire wrapping tool
c. Tools consumables
i. Solder
ii. | Solder wick
iii. | Permanent marker
d. Instructions
i. Solder all header pins onto the shield
ii. | Label special grove connector sockets (S1-S9)
iii. | Solder S1-S9 onto the shield as shown below. The receptacle pins are
| slightly smaller than the holes in the perfboard so you will need to bend
| them out slightly.


iv. | Follow the schematic when connecting wires. Tips:
1. Wire wrapping is easier than soldering to the pins on the grove
| connectors. Where multiple connections to a single point are required, try to make the multiconnection point be something that you can wire wrap.
2. If you are unsure what a wire wrapping tool is or how to use it, by
| searching for “wire wrapping electronics tutorial” you will find some good information.
3. As you can see from the schematic, there are a lot of connections
| routed to many different places. This will result in the wires on the

schematic forming a sort of ratsnest. To help manage this complexity, it is recommended you try to color code the wires as best as possible. One schema to do so is:
a. Ground: Black
b. Voltage Source: Red
c. Signal: Else
4. A soldering iron with a fine pointed tip will make the job easier.

### 9. Controller Module

a. Materials
i. Arduino mega 2560
ii. | USB A-to-B cable
iii. | Finished arduino mega protoshield module
iv. | Grove base shield
v. Raspberry Pi 2
vi. | 8 GB SD card
vii. | Raspberry Pi 2 power supply
viii. | 20’ ethernet cable
ix. | Touch screen display
x. 2x13 ribbon cable
xi. | small .5” screws x8
xii. | Reed Reay
b. Tools
i. Hot glue gun
ii. small screwdriver
c. Tools Consumables
i. Hot glue
d. Instructions
i. Screw the arduino into the electronics panel
ii. | Place the perfboard on the arduino mega
iii. | place the grove shield on top of the perfboard
iv. | Screw the raspberry pi into the electronics panel
v. Screw the screen into the acrylic front plate of the food computer and
| connect to the raspberry pi with the ribbon cable
vi. | Load the image onto the SD card and place in the raspberry pi
vii. | Connect the Arduino usb cable to the raspberry pi
viii. | *Note, connect the signal line of the reed relay to pin 22 on the Arduino.
| The power and ground are used to break the connection on the EC
| sensor so that there is not noise when the pH sensor is recording.
| Connect the power and ground of the EC to the power and ground out of
| the reed relay.

### 10. Air Sensors Module

a. Materials
i. Cozir CO2 Sensor
ii. | Grove Digital Light Sensor
iii. | Grove Temperature/Humidity Sensor Module
b. Tools
i. Screwdriver
ii. | small .5” screws
iii. | 1”x1” square of .5” thick pvc
iv. | .75”x2.5” rectangle of .5” thick pvc
v. 1” stamped angle section
vi. double sided foam tape, about 5”x1”
c. Instructions
i. The temp/humidity and light sensors sit between the circulation fan and
| the vent fan louver.
ii. | First start by taping the rectangle of PVC lengthwise to the angle, so that
| the end of the rectangle is flush with the same surface as the angle.
iii. | Next apply tape to the back of the angle and place it so that it is flush with
| the louver and 6” above the lowermost surface of the window to the grow
| chamber.
iv. | Next tape the temperature/humidity center vertically on the front face of
| the angle below the cantilevered PVC rectangle (see below).
v. Next tape the light sensor to the top of the PVC rectangle so that it is at
| the very edge. This ensures that nothing will obstruct light from reaching
| the sensor
vi. | Finally, tape the 1”x1” square of PVC to the back of the CO2 sensor and
| then tape to the electronics panel right above the circulation fan
vii. | Wire the sensors to the ports specified in the schematic

### 11. Lights

a. Materials


i. one rope of white LEDs
ii. grove cable
b. Tools
i. Knife
c. Tools Consumables
i. Clear shipping tape
d. Instructions
i. The strip of LEDs will go around the circumference of the electronics
| panel. Starting above the wire management box and wrapping
| counterclockwise, stick the strip to the edge of the PVC. Use intermittent
| clear tape to hold the leds onto the panel.
ii. | As per the schematic, connect the power and ground of the strip to the
| white and yellow wires of a grove connector. The red and black will go to
| the second LED strip on the LED panel assembly.
12. Grow LED Panel and Camera Assembly
a. Materials
i. two grow LED panels
ii. 18” stamped flat
iii. 24” stamped flat
iv. 8” stamped flat v. 19.5” ⅜-16 threaded rod vi. 1.5”x1.5” PVC square
vii. Webcam and wire
viii. small .5” screws
ix. 3” stamped flat
b. Tools
i. ⅜” drill bit
ii. power drill
iii. knife
iv. bandsaw
v. screwdriver
c. Tools Consumables
i. Clear shipping tape
d. Instructions
i. Start with two panels


ii. Unscrew the covers and save the screws iii. Take the 18” section of stamped flat to the shop and cut a tab on either end the width of the hole (⅜”). Sand so that there are no sharp edges.


iv. Align the 18” section with one panel so that the plug is to the right. Drill two holes and bolt the stamped flat to the light plastic enclosure.


v. Place a second panel adjacent to the in the orientation below (both plugs facing back) and attach the 24” section to the front face the same way.


vi. Take the 8” section and attach to the side with the plugs.


vii. Drill a hole through the center seam of the two panels. This will be used for the camera mount.

viii. Take the PVC and drill a .75” hole through the center. Drill two small (.125”) holes in the bottom of the 3” stamped flat section


ix. Clip the corners of the webcam where the mounting holes are. This creates room for the screws. Place the webcam on the PVC block so that the lens goes through the center. Screw through the corners to secure the webcam to the block


x. S

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
xi. Place the webcam assembly through the center so that the uppermost hole on the stamped flat aligns with the center hole through the plastic enclosures. Bolt through all three and tighten. Replace the coverings on each LED panel and it is ready for assembly.


xii. Assemble the support rod. Screw a nut from each edge of the rod 5” in. Place a washer and second nut and tighten. Place one more nut on each side and thread through the frame. Tighten with nuts on the outermost edge. This is what the front of the lights rests on.


The tabs are used to hold the other side of the lights to the frame.


Finally lay a strip of leds on the face of the led panel. Extend the LED wires and pass them through the hole in the electronics panel upper corner. Connect to the black and red wires of the other LED grove connector. Place both in port S2.

14. System Testing / Debugging
Upload the microcontroller code to the arduino mega 2560. This code can be found on github under OpenAgInitiative/grocontroller/src.For initial testing, use the arduino serial monitor. The easiest way to do this is with the arduino IDE. Assuming the code is uploaded to the arduino and the serial monitor is open, there will be a giant stream of text running down the screen. This console is a window into how all sensors and actuators are interfaced with. A single stream message looks something like this:

“{"GTYP":"Stream","SWPH 1":6.9,"SWTM 1":25.4,"SWEC 1":2.6,"SLIN 1":33,"SLPA 1":0.73,"SATM 1":24.7,"SAHU 1":31.3,"SACO 1":400,"SATM 2":25.2,"SAHU 2":39.0,"SGSO 1":0,"SGWO 1":1,"AAHE 1":0,"AAHU 1":0,"AAVE 1":1,"AACR 1":1,"ALPN 1":0,"ALPN 2":0,"ALMI 1":1,"GEND":0}”

This is a message that contains a sequence of instruction codes:
- "GTYP":"Stream" This message type is a stream message.
- "SWPH 1":6.9 The 1st Sensor of Water PH is reporting a value of 6.9
- "SWTM 1":25.4 The 1st Sensor of Water Temperature is reporting a value of 25.4 degrees C
- "SWEC 1":2.6 The 1st Sensor of Water Electrical Conductivity is reporting a value of 2.6 mS/cm
- "SLIN 1":33 The 1st Sensor of Light INtensity is reporting a value of 33 lux
- "SLPA 1":0.73 The 1st Sensor of Light PAr (Photosynthetically Active Radiation) is reporting a value of 0.73 umol/(s*m^2)
- "SATM 1":24.7 The 1st Sensor of Air TeMperature is reporting a value of 24.7 degrees C
- "SAHU 1":31.3 The 1st Sensor of Air HUmidity is reporting a value of 31.3 % relative humidity
- "SACO 1":400 The 1st Sensor of Air CO2 is reporting a value of 400 ppm (parts per million)
- "SATM 2":25.2 The 2nd Sensor of Air Temperature is reporting a value of 25.2 degrees C
- "SAHU 2":39.0 The 2nd Sensor of Air HUmidity is reporting a value of 39.0 % relative humidity
- "SGSO 1":0 The 1st Sensor that is Generally detecting if the Shell is Open is reporting 0 (false)
- "SGWO 1":1 The 1st Sensor that is Generally detecting if the Window is Open is reporting 1 (true)
- "AAHE 1":0 The 1st Actuator that is an Air HEater is reporting 0 (off)
- "AAHU 1":0 The 1st Actuator that is a Air HUmidifier is reporting 0 (off)
- "AAVE 1":1 The 1st Actuator that is an Air VEnt is reporting 1 (on)
- "AACR 1":1 The 1st Actuator that is for Air CiRculation is reporting 1 (on)
- "ALPN 1":0 The 1st Actuator that is a Light PaNel is reporting 0 (off)
- "ALPN 2":0 The 2nd Actuator that is a Light PaNel is reporting 0 (off)

- "ALMI 1":1 The 1st Actuator that is for Light Motherboard Illumination is 1 (on)
- "GEND":0 End of message

The first thing to test is whether or not all the sensors are reporting correctly. These sensing point values are generally representative of ambient conditions (where the light panels are turned off). Usually sensing points that are attached to the same sensor will be incorrect. Here is a list that indicates which sensing points are matched to which sensor:
- DFR01610300 SWPH 1, SWTM 1, SWEC 1
- This sensor “module” is actually 3 separate sensors that have dependencies on each other so we lump them into the same module. These come from DFRobot and each sensor has its own circuit board that is labeled. To get more info about this sensor go to the DFRobot website and use their associated SKU numbers (0161 and 0300). Note: 0300 is a package with Temperature and EC.
- TSL2561 SLIN 1, SLPA 1
- Adafruit has some nice info about this.
- DHT22 SAHU 1, SATM 1
- Adafruit has some nice info about this.
- GC0011 SACO 1, SAHU 2, SATM 2
- Cozir has some nice info about these. This sensor has its own microcontroller onboard. To communicate with it you can send the command “SACO 1 C <msg>”. More on this soon…
- Limit switch SGWO 1
- Functions like any switch
- Magnetic switch SGSO 1
- Functions like any proximity switch

Once all the sensors are up, the next thing to do is test the actuators. By typing the actuator instruction code, id and value into the console, that will set that actuator to that value. Be sure the console is set to “Newline” and “9600 Baud” in the lower right hand corner. Here are a few examples:
- AAHE 1 1 turn ON the air heater actuator
- AAHE 1 0 turn OFF the air heater actuator
- ALPN 1 1 turn ON the 1st light panel actuator (the grow lights)
- ALPN 2 1 turn on the 2nd light panel actuator (the led strip)
- AAHU 1 1 turn on the air humidifier actuator

It is a good idea to go through all the actuators and make sure they can turn on and off. Once this is done, replug the usb cable back into the raspberry pi.

Now, configure the controller (Raspberry Pi). Download the pi image from the OpenAgInitiative github. Upload it to an SD card. Plug it into the pi. Assuming the image has been downloaded onto the SD card and once the ethernet cable is plugged in it is likely the bot will just connect to the internet and get an IP address. Acquire a usb keyboard and plug it into a free USB port on the raspberry pi. Assuming you the touch display is connected to the pi there will be a screensaver that is a picture of veggies. Close this out by using the “ctrl + w” keyboard shortcut. Note: you have 60 seconds before the screensaver pops back up, in which case you will need to “ctrlw” it again. Once the screensaver is closed navigate to the raspberry pi’s terminal: Menu>Accessories>Terminal and type the command “ifconfig”. After typing this command look in the paragraph to the right of eth0 and you should see a string of text that looks like “inet addr: 12.456.7.89”. The string of numbers separated by the periods is the bot’s IP address. This is the IP address used to connect the user interface to your specific bot.

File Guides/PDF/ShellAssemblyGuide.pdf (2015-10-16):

Cutting the Insulation Foam

If you are cutting using a standard table saw, I found that it is easier to cut the large 4’x8’ sheet into sections slightly larger than the ultimate panel dimensions. This both makes each individual panel easier to work with and provides a clean opposite to the final cut width.


Once the sheets has been cut into the approximate panel dimensions, you can then cut the actual dimensions in the CAD.

Front Panel: 25.6875” x 30.625”
Back Panel: 25.6875” x 30.625”
Side Panel: 19.375” x 30.625”
Top Panel: 21.375” x 25.6875”

Next you need to cut the window into the front panel. I created a jig but a ruler works just fine. From the upper left corner as the origin of a cartesian system, measure 3.25” in the +x direction and 3.1875 in the y direction. This will be the upper left corner of the window. The dimensions of the window are 18.75” wide by 19.3125” tall. See picture below for relative orientation if confused. Cut out the window and discard the scrap.


Front Panel, Back Panel, Side Panel, and Top Panel

Gluing Together the Foam Box

*Follow the video and consult the CAD for better visuals on how to assemble the box

Using hot glue, lay down a continuous zigzagging line about an inch wide along one of the edges to be glued.


Firmly push the mating panels together and hold while the glue dries. The front and back panels should be on the outermost face, while the side panel sits between the front and back panels. The top panel should be placed on the top of the front, side, and back panels.


Taping the Edges

Once the box has been glued together, the exposed edges where the yellow insulation foam can be seen need to be covered up. Using foil tape, cover all exposed edges so that no foam can be seen.


Cutting the Corruplast

Because the panel dimensions of the corruplast are larger than the foam, cutting approximate dimensions is not possible. In fact, the width dimensions of the panels add up perfectly to 8’ or 96”. So cutting along the exact lines is the only way to make use of the whole panel. Note, due to the width of the saw blade, each panel will be missing between 1/16” ⅛” of material. This has not been a problem for us though.


The exact dimensions are as follows:

Front Panel: 26.625” x 32.5625” Back Panel: 26.625” x 32.5625”
Side Panel: 21.375” x 32.5625”
Top Panel: 21.375” x 26.4375”

Like the foam, next you need to cut the window into the front panel. I created a jig for this as well but a ruler works just fine. From the upper left corner as the origin of a cartesian system, measure 3.5” in the +x direction and 3.875 in the y direction. This will be the upper left corner of the window. The dimensions of the window are 19.75” wide by 20.3125” tall. Cut out the window and discard the scrap.

Gluing the Corruplast to the Foam Box

We make use of Loctite spray adhesive with the web spray nozzle feature to get good coverage.


The directions on the bottle specify that each component get two coats of adhesive, spaced about 2-5min apart. The general procedure involved applying a coats of adhesive to both the corruplast and foam then carefully sticking the corruplast panels onto the foam box.

Refer to the CAD model and video to see orientation of the corruplast sheets and procedure of gluing. There will be a lip left on the bottom left side edges of the foam box. This is so that corruplast covers the PVC sheets for aesthetic purposes. When applying adhesive, be careful not to get too close to the hanging edge. The glue dries nontacky so it isn’t much of a problem if a little glue gets on these regions. For alignment purposes, see that the corruplast creates a ~.5” rim around the center window. This will be where weatherstripping goes.

Cutting the Window Plate

Using a tablesaw, cut a sheet of ⅛” polycarbonate to 19.75” x 30.3125”. Round the edges with a wood file and set aside. This will be the window plate.

Creating the Window Seal and Magnetic Connection

Using the doublesided highbond foam tape, stack two of the 0.75” neodymium disk magnets and tape one stack on each of the corners of the window, and in the middle of each of the edges of the window. Make sure all the magnets are the same polarity facing outward.


Place strips of weatherstripping between the magnets in the .5” gap left by the corruplast.


Finally, foam tape magnets to the outside face of the window plate by aligning the window plate with the window in the shell, and placing the magnets over the stacks below.



Window Off | Window On

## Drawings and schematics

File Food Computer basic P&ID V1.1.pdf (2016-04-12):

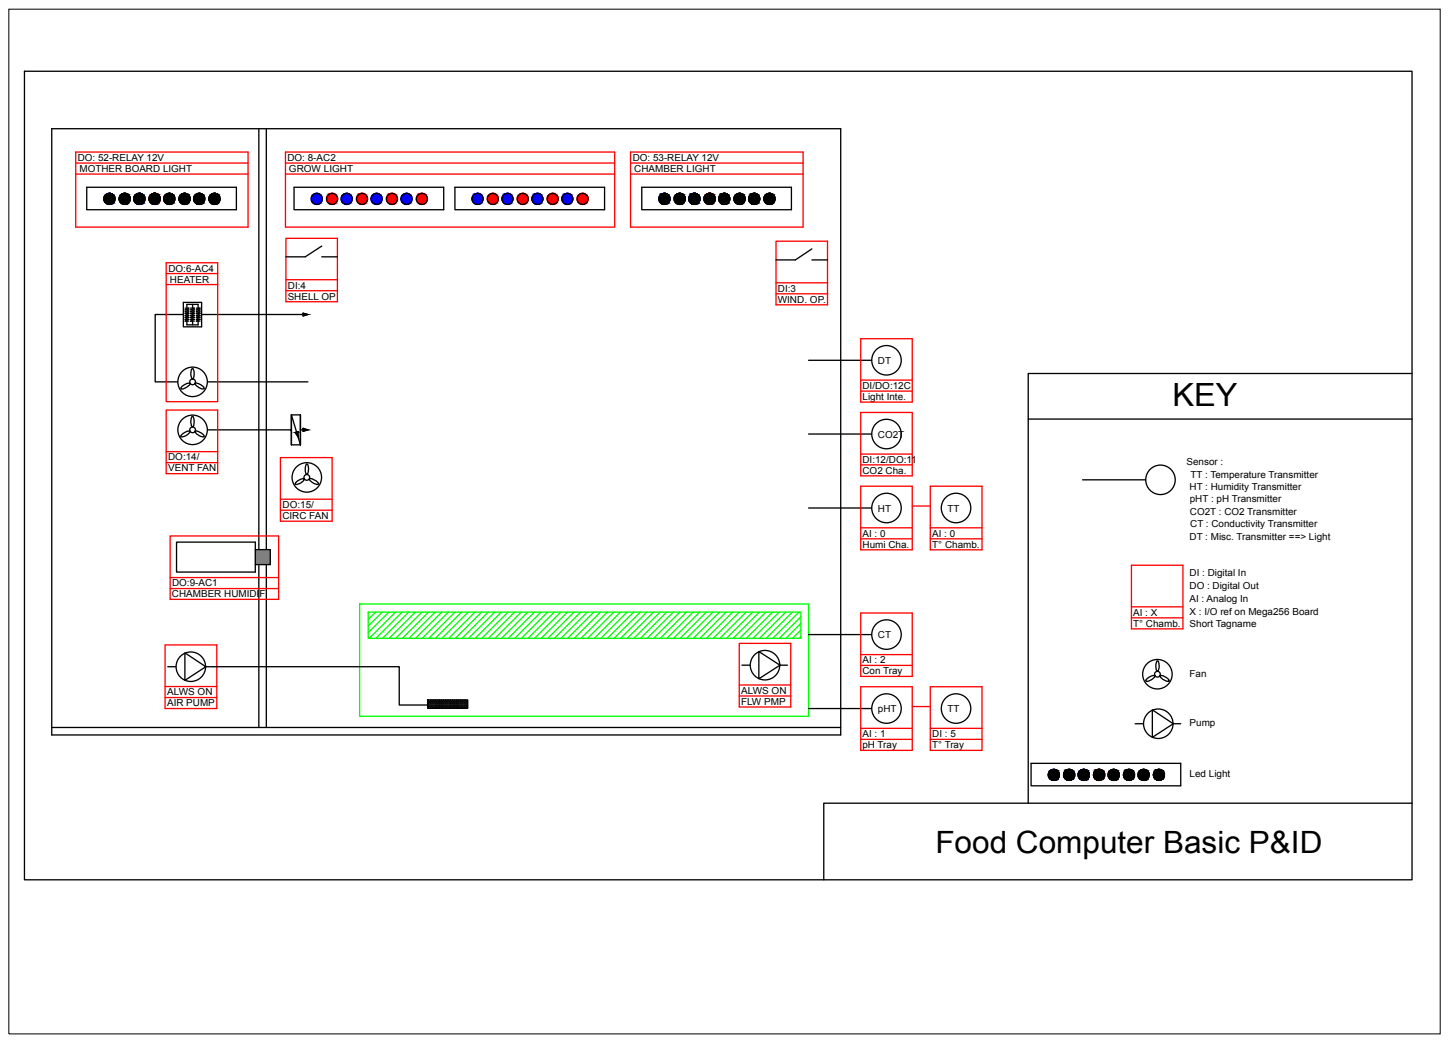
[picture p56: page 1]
VENT FAN; CIRC FAN; AIR PUMP; ALWS ON; FLW PMP; GROW LIGHT; pH Tray; CHAMBER LIGHT; DO: 53-RELAY 12V; Con Tray; T° Tray; Humi Cha.; CO2 Cha.; Light Inte.; T° Chamb.; SHELL OP; WIND. OP.; Led Light

DO: 52-RELAY 12V
MOTHER BOARD LIGHT

Sensor :
TT : Temperature Transmitter
HT : Humidity Transmitter
pHT : pH Transmitter
CO2T : CO2 Transmitter
CT : Conductivity Transmitter
DT : Misc. Transmitter ==> Light

DI : Digital In
DO : Digital Out
AI : Analog In
X : I/O ref on Mega256 Board
Short Tagname

DO:9-AC1
CHAMBER HUMIDIF

Food Computer Basic P&ID

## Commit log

2015-10-16 Create Bill of Materials
2015-10-16 added electronics panel schematic
2015-10-16 added BOM excel
    [BOM food computer.xlsx]
2015-10-16 upload CAD
    [Base SubAssem.SLDASM, Double magnet SubAssem.SLDASM, Food Computer Assembly.SLDASM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]
2016-04-12 P&ID by Martin van Gansberghe
    [Food Computer basic P&ID.dwg]
2017-03-07 Reorganize files
    [BOM food computer.xlsx, BOM.xlsx, Base SubAssem.SLDASM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]
2017-03-09 Add Dimensions of PVC Boards
2017-03-12 Update missing.md
    Includes adding links to purchase parts and updating details on missing grove items in BOM
